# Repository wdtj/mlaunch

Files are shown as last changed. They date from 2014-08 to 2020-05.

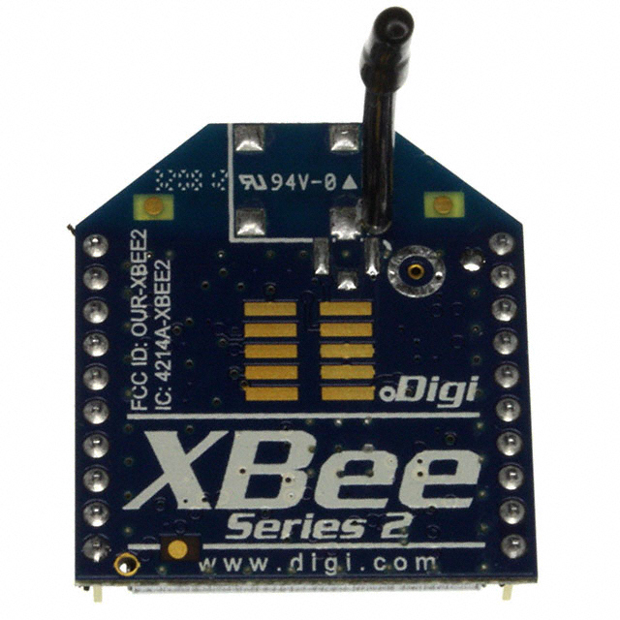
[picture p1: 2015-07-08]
XB24-Z7WIT-004.JPG

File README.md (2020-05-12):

# mLaunch launch control system

mLaunch is a mesh network based model rocket launch system designed to handle up to 8 launch pads.  Its primary feature is safety.  Multiple commands are required to enable multiple relays in the launch circuit.  It also provides feedback on igniter resistance and battery voltage.  Using a mesh network, allows near launch pads to relay launch commands to launch pads further away.

See file Report on [Project mLauch Version 3.0.pdf](Report%20on%20Project%20mLauch%20Version%203.0.pdf) for an overview of mLaunch

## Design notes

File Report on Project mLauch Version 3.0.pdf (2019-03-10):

Wayne Johnson
CSCI5991-001
ID #4348421
joh09024@umn.edu
Independent Study
6/20/2017

# Report on Project mLauch Version 3.0

## Introduction

Did you ever play with model rockets as a kid? It’s a fun hobby that lead to many different areas of Science, Technology, Engineering, and Math (STEM). Building and flying a rocket can involve kinematics (the branch of physics involving motion), aerodynamics, chemistry (as in rocket fuel), even electronics and software engineering as well as many manufacturing technologies. This project is based in the areas of electronics and software development.

A typical model rocket is shown in Figure 1. The rocket has a motor that uses black powder (AKA gun powder) or on larger rockets, Ammonium Perchlorate Composite Propellent (APCP), the same rocket propellent the Space Shuttle used. It also uses a parachute or streamer to help recover the rocket and fins to keep it stable during flight. When the rocket flies to it’s highest altitude, a small ejection charge in the end of the motor pops off the nose cone and deploys the parachute.

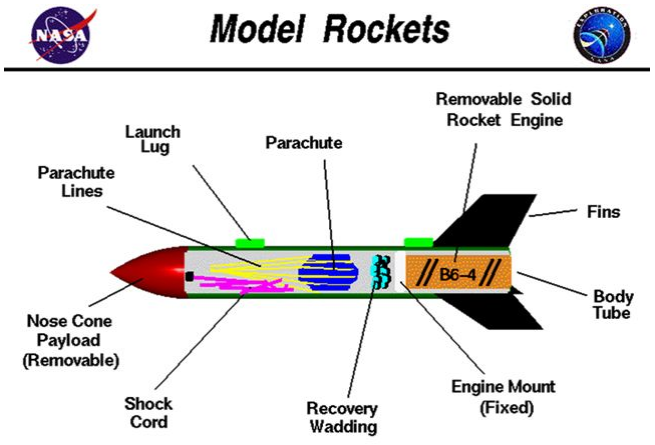
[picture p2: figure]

Figure 1 - Typical Model Rocket

Model rocketry has also grown up with the times. In years past, flying a “Big Bertha” on a class “C” engine was just about the peak of power in the sport. Nowadays, model rockets have developed into high power rocketry. High power rockets as large at 29 feet tall being powered by class “M” class engine have become quite common to the adult high power rocket hobby. To put things in perspective, each letter in the engine classification system is twice as large as the previous. This can lead to an “M” engine that produces as much as 2500 pounds of thrust, and weighing in (just the motor) at 5302.00 grams (12 pounds for the metrically challenged).

As an example of one such rocket launch: Locomotive Breath (a reference to a Jethro Tull song). This rocket was built out of a 16 gauge aluminum pipe and 18 gauge aluminum fins, a single use “P” rocket engine, a pair of parachutes, and a significant amount of on-board electronics such as altimeters and radio tracking equipment. The preflight modeling indicated that it would reach 17,000 feet, while reaching mach 2.3. Figure 2 is picture at launch, the rocket in flight, and what remained after a mid flight failure (as around Mach 1). A post-mortem indicated that one of the fins sheared off in mid flight.

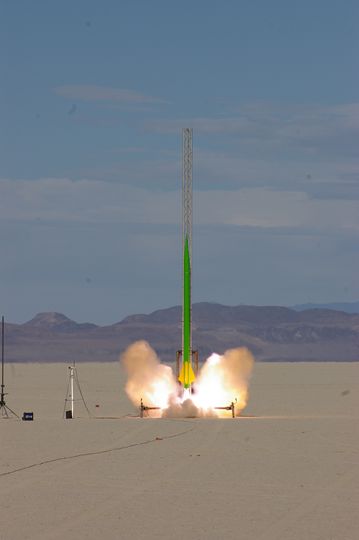
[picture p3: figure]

Figure 2 - Locomotive Breath

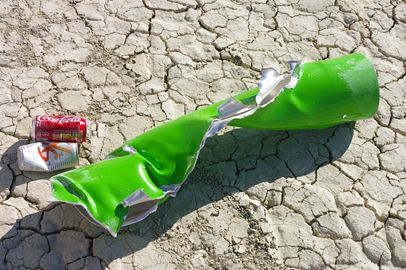
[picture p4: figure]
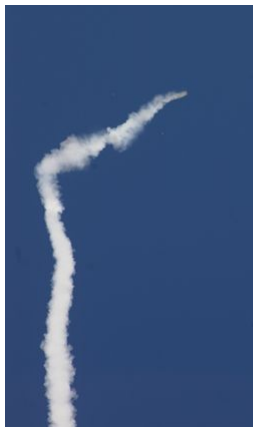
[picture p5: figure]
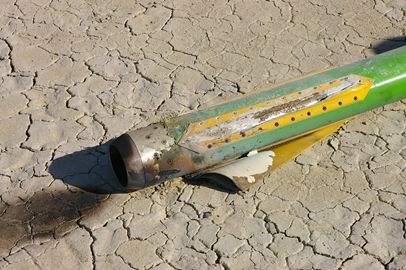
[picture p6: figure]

As you can see, high power rocketry can be hazardous. It is the goal of Tripoli Rocketry Association, as well as the National Association of Rocketry (NAR) to keep the sport safe, as well as fun. Both organizations represent over 10,000 model and high power rocketry enthusiasts around the globe.

You can not simply walk up to a rocket and flick your BIC under the engine. Rocket engines are ignited electronically, by running current through a thin nichrome wire installed in the engine core. The heated wire ignites a small amount of pyrogen, which in turn ignites the rocket fuel. Figure 3 depicts a simple launch system.

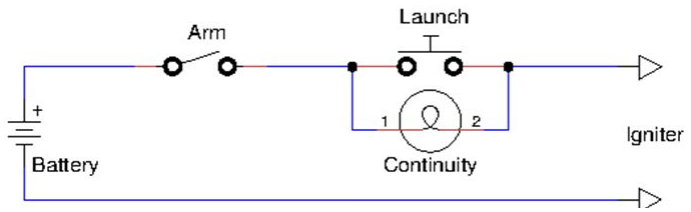
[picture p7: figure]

Figure 3 A Simple Launch System

Because of these dramatic increases in scale in high power rocketry, new safety procedures have been developed. It’s quite common for an class M motor based rocket to be launched 1/4 mile (or more) away from the nearest human or structure. Many different schemes have been used to perform this. Everything from running a 1/4 mile long wire out to the rocket, to using radio control airplane parts. One person used a garage door remote control as a means of closing a relay at the launch pad, to light their rocket. There are been many other schemes, some quite a bit more problematic and unsafe as well. As you can see, there is room for improvement. The mLaunch project was launched to create a safe, dependable, and low cost solution to this problem.

## History of mLaunch

The first version of mLaunch (1.0) was developed in 2004 to augment and eventually replace the launch control system used by Tripoli Minnesota, a local high power rocketry club. For the previous 15 years, Tripoli Minnesota had been using a wired relay based launch controller that included a control panel with toggle switches, a long and heavy wire cable, and remote relay boxes for pads located farther away. A high level overview of this system can be seen in Figure 4.

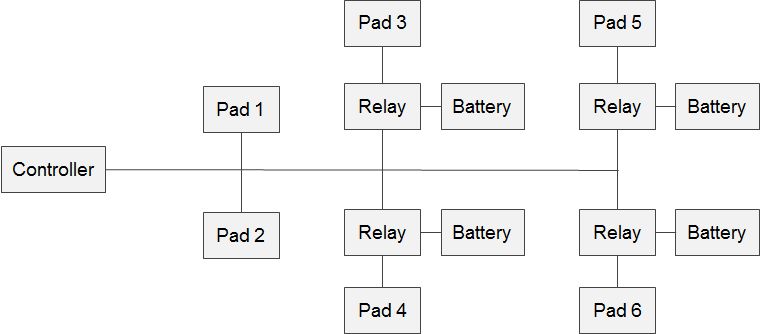
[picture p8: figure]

Figure 4 - Tripoli Wired Launch System

The wired launch system presented several problems. Besides being big and cumbersome to set up, having a 40 lb spool of wire, it also had many points of failure, batteries being low, connections being bad, relay contacts getting worn. It also had limited ways of diagnosing an issue. Many times club members would be seen probing around the pads with a volt meter trying to identify just why their rocket wouldn’t go.

### mLaunch 1

At this point, two new technologies were making it to market. Cheap and easy to program single chip microcomputers, and a new Maxstream XBee wireless module based on the Zigbee mesh network protocol. These two technologies were put together to create a wireless launch system. At the pad end, a XBee transceiver (AKA Modem), an Atmel ATMega8

System-on-a-Chip, push-button switches and LEDs to check for igniter continuity, and a pair of relays to actually launch the rocket.

At the Launch Controller end, is another XBee transceiver and ATMega8 as well as push buttons, and LEDs to show status of the pads. See Figure 5.

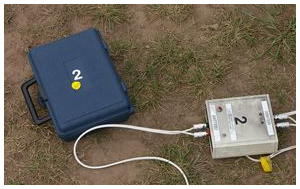
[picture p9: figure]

Figure 5 - Version 1 pad box.

As a first attempt, this system worked quite well and remained in production for over 7 years. It’s still around and servers as a backup system. Unfortunately the system was built using home made printed circuit boards (many of which had to be patched due to etching flaws, as well as a “rats nest” of wired interconnections between PC board and relays, LEDs, push-buttons, and banana jacks (for power and pad connections). With the desire to make the system easier to manufacture, version 2 was planned.

### mLaunch 2

mLaunch2 brought many new production class enhancements. It was a first attempt at surface mount technology, used professionally made PCBs, Digi (which bought out MaxStream) XBee Series 2 modules, and a Atmel Dragon JTAG & IDE programmer/debugger. Many factors combined to doom this version, the XBee Series 2 modules were buggy, the new SMT technology had a large learning curve, and the ATMega8 chip was cramped for RAM space leading to stack corruption and some very frustrating and confusing software failures. The project got shelved.

### mLaunch 3

Knowing the end-of-life was approaching for the version 1 system, a fresh start was made on a new version 3 in 2012. This new design included more SMT parts, a bigger Atmel Mega32 Series CPU, A new PCB Supplier (the earlier one went out of business), a new Atmel ICE/JTAG3 professional class programmer & IDE.

This version was completed, and programmed, and put into production in the spring of 2014.

## mLaunch 3.0 Requirements

Some of the requirements for mLaunch 3.0 were (and still are):

- Easy to make, single board construction
- Minimal circuit connections, no rats nests or wiring harness
- More reliable components
- Dual automotive grade relays which are field replaceable
- 20 amp automotive class circuit breaker instead of fuses to protect from igniter (and other) short circuits.
- Reverse voltage protection & static “surge” protection
- More detailed remote statistics such as actual ignitor resistance and pad end battery voltage via a 8x20 LCD to display
- Dual circuit per pad box (to reduce costs)
- 8 Pad support
- CPU powers up in inert state preventing accidental relay closures when started.
- Ultra bright tri-color (red/green/yellow) LEDs, 180-450 lumen, visible in direct sunlight (most of the time).

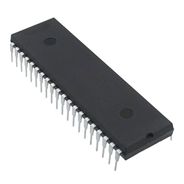
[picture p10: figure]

## ATMega32A CPU Specification Highlights

- Up to 16MIPS Throughput at 16MHz
- 32Kbytes of In-System Self-programmable Flash Program Memory
- 1024Bytes EEPROM
- 2Kbytes Internal SRAM
- Two 8-bit Timer/Counters, One 16-bit Timer/Counter
- 32 Programmable I/O Lines
- 8-channel, 10-bit ADC
- Programmable Serial USART
- $5.88 MSRP

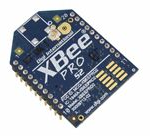
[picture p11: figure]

## XBee-Pro™ ZB S2B Specification Highlights

- 2.4 GHz Transceiver (Transmitter/Receiver)
- Extended-range ZigBee, Through-hole, Mesh Networking
- 2 miles / 3.2 km Range (YMMV, outdoors, with a parabolic antenna, and the wind at your back). Expect 1/4 mile.
- $28.00 MSRP
- 250 Kbps Data Rate

## Mesh Networking

Unlike the MaxStream XBee Series 1, the Digi XBee Series 2 supports true mesh networking. This means that if a node in the network receives a message for some other node, it will pass that message on to it’s nearest neighbor that is nearer to the final destination. Using a mesh network in mLaunch allows us to place launch pads out of the direct range of the launch controller, but as long as there are one or more nodes (i.e. pads) connected between the controller and the remote pads, command and status messages can still be sent. This is represented in Figure 6

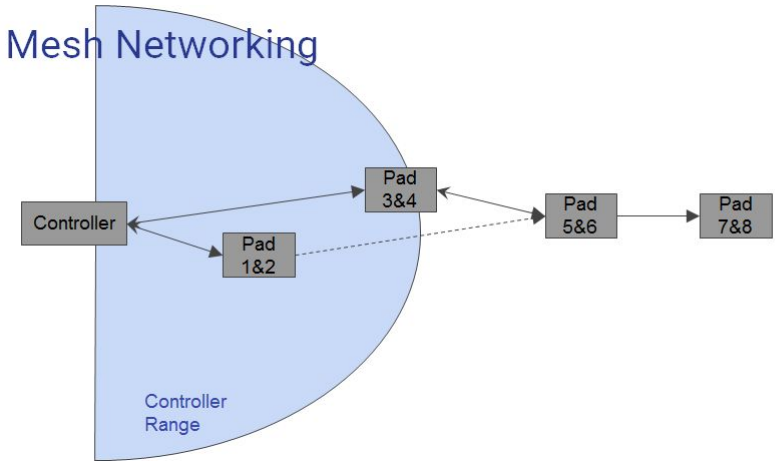
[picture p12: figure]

Figure 6 - mLaunch Mesh network

## Block Diagrams

The mLaunch system consists of two types of modules. One Launch Controller box, and up to 4 pad boxes.

### Launch Controller

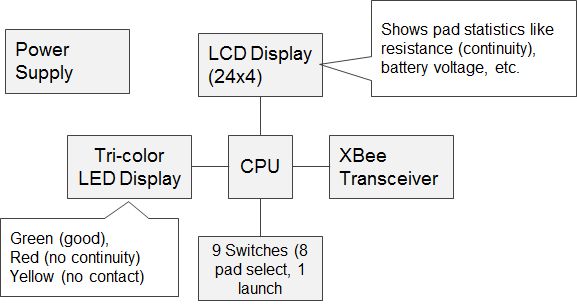
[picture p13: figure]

Specific schematics for the Launch Controller are available at https://github.com/wdtj/mlaunch/blob/master/controller30/controller30r3.pdf

Power Supply
The mLaunch Launch Controller power supply is pretty standard. It accepts 6-18 volts input and provides both regulated 3.3 and regulated 5 volt outputs. One interesting note is that the input to the power supply contains a bridge diode. A bridge diode is normally used to rectify AC inputs into DC. Using in here allows the Launch Controller to be mis-connected to a battery and it will still work. Also included in the input circuit is an 18v varistor to protect the circuit from static discharge along the power input path.

CPU
The mLaunch launch controller CPU is an Atmel ATMega32A microprocessor on a chip. The CPU runs off the 5 volt power supply and uses a 16Mhz crystal for a CPU clock. Although the ATMega32A has a built in capacitive clock circuit, it is not accurate enough to control the serial communications connection with the XBee module at 9600 baud. In addition, the ATMega32 is connected to a 10 pin 1mm pitch header. This is used for programming the CPU as well as debugging. Details on the ATMega CPU architecture and programming are available in the ATmel supplied ATMega32 documentation at https://github.com/wdtj/mlaunch/blob/master/atmega32A.pdf.

XBee Transceiver
The XBee transceiver is the heart of the system communications. These modules are pre-programmed with either XBee coordinator or router software. There can be only one coordinator in the XBee network, and this device coordinates the mesh network. The XBee uses a 3.3 volt power supply. In order to translate between the CPU’s 5 volt signals and the XBee 3.3 volt signals a simple voltage shifter is used. By default the XBee operate at 9600. The module is also preprogrammed to run in API command mode (vs AT command mode) to make it easier to communicate with the CPU. Details on the XBee communication commands and other details are available in the Digi supplied XBee user’s guide at https://github.com/wdtj/mlaunch/blob/master/XBeePro2.pdf. Connection to the XBee transceiver is via the CPU’s USART on the RXD and TXD pins.

LCD Display
The LCD display is a LCM-S02004DSR from
Lumex. Pinout and electrical specs are here:

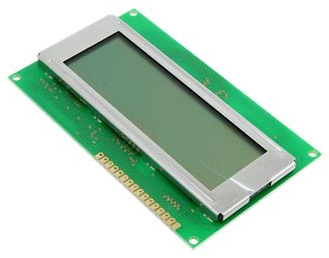
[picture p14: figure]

https://github.com/wdtj/mlaunch/blob/master/LCM-S02004DSR.pdf
It uses an industry standard LCD controller HD44780U. You can find this spec at https://github.com/wdtj/mlaunch/blob/master/HD44780.pdf The LCD requires 5 volt power and 5 volt data signals, but since the CPU is already running at 5 volts this is not an issue. The LCD uses 8 parallel lines to send data/address information to/from the LCD display, along with 3 control lines. The CPU port PA 8 bit port provides the basic parallel data, and the CPU’s PD2, PD3, and PD4 lines provide control signals. Basically a command or data byte is written on the PA port and the E pin is strobed to send data to the LCD. Consult the HD44780 document for more specific details.

Switches
9 pushbutton switches are connected directly to input pins of the CPU. These are pulled high (a logic 1 state) by internal (to the CPU) resistors, and pressing one of the buttons causes the input to be grounded (pulled low) to present a 0. Software needs to “debounce” these switches because the mechanical contacts in the switch can vibrate on contact producing an intermittent signal for a few milliseconds. The software, when detecting a switch that is opened or closed will need to check again a few milliseconds later to verify it’s still in that state. The pad enable switches use the CPU’s PB port (8 pins) and the PC7 pin for the launch button.

LEDS
The LEDs have 3 different LED circuits in one package. Red, green, and yellow. This amounts to 24 different circuits required to drive all LEDs, more than are available on the CPU. To get around this, there are 3 TI TLC5917 LED drivers in the circuit. This driver is basically 3 8 bit shift registers, wired in series. To turn on or off an LED, the appropriate bit is output into the input (SDI) of the first driver register and the driver clock signal (CLK) is strobed. Then the next bit, etc. until all 24 bits have been written. All the red LEDs are written in the first byte, all yellow on the second byte, and all green in the third byte of the 24 bits. Specifications for the TLC5917 driver can be found at https://github.com/wdtj/mlaunch/blob/master/tlc5917.pdf. The LED driver is connected to the CPU’s PD5 (CLK), PD6 (LE), PD7 (SDI), and PC0 (SDO) pins.

## MLaunch Pad

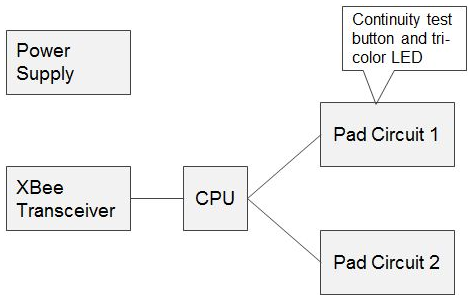
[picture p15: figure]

Specific schematics for the Pad is available at https://github.com/wdtj/mlaunch/blob/master/pad30/pad30r4.pdf

Each pad modules is capable of managing 2 pads and thus has 4 relays (2 per pad), 2 continuity test buttons, and 2 tri-color LEDs as well as circuitry to measure the voltages across the ignitor and a circuit to measure battery voltage.

Power Supply
The mLaunch Pad power supply is also pretty standard. It accepts 6-18 volts input and provides regulated 3.3 volt output. Again the power supply contains a bridge diode to allow the battery inputs to be mis-connected and also it has an 18v varistor to protect the circuit from static discharge along the power input path. One interesting problem in development, the diode bridge can allow the voltage sensing circuit for the pads ignition to be either above or below the ground voltage of the CPU and it’s integrated ADC. This issue is handled by a set of resistors in that circuit that translate the voltages from the possible +18 to -18 volts to the ADC’s required 0-2.55 volts.

CPU
The mLaunch pad CPU is again an Atmel ATMega32A microprocessor on a chip. The CPU runs off the 3.3 volt power supply and it uses a 16Mhz crystal for a CPU clock. Everything else is the same as for the launch controller. The CPU circuit also contains a resistor bridge that allows the CPUs ADC to measure the battery voltage.

XBee Transceiver
The pad transceivers are preprogrammed as router nodes. Since both the XBee and CPU uses a 3.3 volt power supply no translation is needed. Connection to the XBee transceiver is via the CPU’s USART on the RXD and TXD pins.

Pad Circuit
The pad circuit (x2) contains a ULN2003A darlington transistor driver, which provides enough current to the CPU signal to drive the relay coils. These also protect the CPU from high reverse EMF pulses that are generated as the relays turn off. A network of resistors translate the possible +18 volt to -18 volt continuity signal from the pad into a 0-2.55 volt signal for the CPUs ADC.

In addition, each pad circuit contains a pushbutton switch to test continuity and a tri-color LED to display the results. The pad controls use the following pin assignments:

Function | Pad 1 CPU Pin | Pad 2 CPU Pin
Continuity Detect ADC Input | PA0/ADC0 | PA1/ADC1
BATT+ ADC Input | PA2/ADC2 | PA2/ADC2
Launch Relay | PA3 | PA6
Enable Relay | PA4 | PA7
Red LED | PB0 | PB4
Green LED | PB1 | PB5
Yellow LED | PB2 | PB6
Continuity Switch | PB3 | PB7

## Functional Overview

In order to launch a rocket, first the rocket owner places the rocket on the pad, and connects the pad’s ignition leads to the ignitor in the rocket engine. The owner can then press the pad’s continuity button which will light up green (good continuity) or red (red continuity). There is also a yellow light that indicates low battery voltage.

When the Launch Control Officer (LCO) gets ready to launch the rocket, they press and release a button on the launch controller corresponding to the appropriate pad. The pad’s first relay closes in order to place a small continuity test current through the ignitor. Both the pad and launch controller LEDs light with the continuity status. The LCO then presses the launch button which closed the second relay at the pad. This sends the full battery current through the igniter. When the LCO releases the launch button, the pad is then disabled.
If, before pressing the launch button, the LCO presses the pad enable button a second time, the pad is disabled and returns to it’s initial state..

If, before pressing the launch button, the LCO presses the a second (or more) pad enable button those pads are enabled and their respective LEDs light with their statuses. Then by pressing the launch all the enabled pads are launched.

If, when pressing the pad enable button the first time it’s held down for more than a second, the pad statistics (battery voltage and continuity resistance) are displayed on the LCD display.

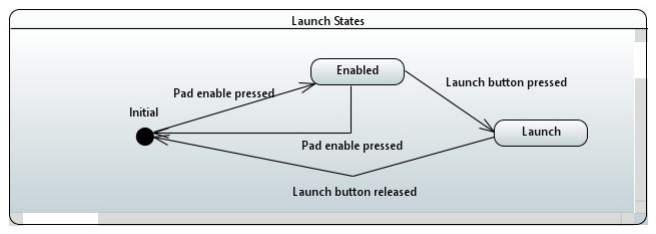
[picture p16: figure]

## Application Level Message Packets

There are relatively few application level packets exchanged. They are kept short to reduce requirements on bandwidth. They do not have any CRC or other error checking/correcting data as these functions are done in the XBee itself. These packets include:

Enable - Enable the continuity checking relay and causes the pad to begin to send back status packets. | Ex where x is a pad number from 1-8
Launch - Closes the launch relay | Lx where x is a pad number from 1-8
Status - Returned by the pad with current information | Sxnn...n where x is a pad number from 1-8, and nn...n is pad status information
Unlaunch - Opens the launch relay | Ux where x is a pad number from 1-8
Disable - Opens the continuity relay and return to normal state. | Dx where x is a pad number from 1-8
Identify - Caused the specified pad to begin flashing it’s green LEDS to identify it for configuration. | I
Assign - Assigns a pad number to that pad. Used for configuration. | Ax where x is a pad number from 1-8

After an Enable command is sent, a watchdog timer is set that will reset the pad if no other request is sent within 10 seconds. This timer is restarted when any packet is received for that pad. To ensure a pad does not reset itself too early, the controller repeats the enable command every second. After a pad receives an Enable message, it begins sending back Status messages every second until the Disable message is received or the watchdog timer resets the pad.

The watchdog timer is used to safe any and all pads in the event the Launch Controller goes away.

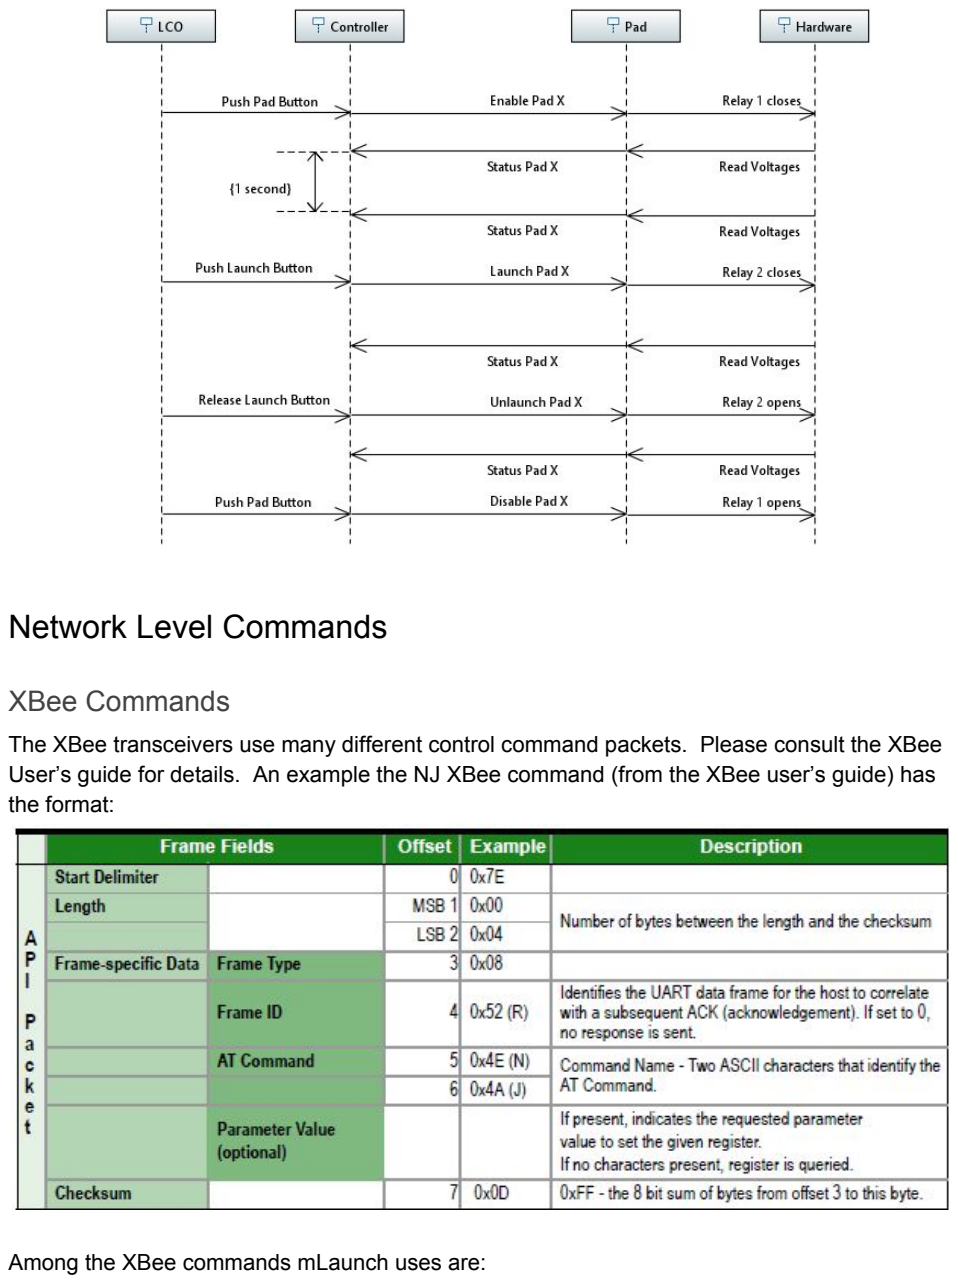
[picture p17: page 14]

## Network Level Commands

### XBee Commands

The XBee transceivers use many different control command packets. Please consult the XBee User’s guide for details. An example the NJ XBee command (from the XBee user’s guide) has the format:

Among the XBee commands mLaunch uses are:

NI | Node Identifier. Set/read a string identifier naming the node.
NJ | Node Join Time. Set/Read the time that a Coordinator/Router allows nodes to join.
NR | Network Reset. Reset network layer parameters on all modules within a network.
ND | Node Discover. Discovers and reports all RF modules found.
NJ | Node Join Time. Set/Read the time that a Coordinator/Router allows nodes to join.
JV | Channel Verification.
VR | Firmware Version. Read firmware version of the module.
JN | Join Notification. Set / read the join notification setting. If enabled, the module will transmit a broadcast node identification packet on power up and when joining.

When the system if first brought up, the Launch Controller initializes all it’s hardware and sends a command to the XBee module to discover it’s network (all the pads). Over the next 5 seconds each powered up pad responds with it’s name and a network address. The XBee devices randomly staggers the responses to prevent everyone from answering the discovery broadcast at once. As each pad is identified, the Launch Controller LEDs for that pad set are turned green. When the 5 second wait is done, the controller turns off all the LEDs and is ready for business.

During operation, if any pad joins the network, the Launch Controller will receive a Discovery notification from the XBee device and add that pad to it’s operational list.

### XBee Data

In addition to commands sent to the XBee transceiver, application data is sent. Data is wrapped in a XBee API data packet. These data packets can then be marked to be sent to a specific node using a XBee Explicit Addressing ZigBee Command Frame, or can be sent to all devices. All communications are via explicit addressing

## Software Design

The ATMega system are very minimal. They do not contain an operating system, therefore all software is written on “bare metal” and in machine code. To this end, the majority of the software is asynchronous in nature, operating on a set of Finite State Machines (FSM). When a packet is to be sent to the XBee transceiver, the message is queued up and the USART’s interrupt system then controls when the next character is to be sent. There is also a FSM managing pad controls, switch closure detection (debouncing), and the communication protocol to the XBee.

### Modules

Software is broken into the following “projects” or modules: Utilities
Pad
Controller

Utilities
The Utilities module contains common code and drivers including the following:
ADC Driver | Driver for the ATMega internal Analog to Digital Converter
LED Driver | For use with the TI TLC5917 LED drivers
OLED/LCD Driver | For use with the Lumenx (and other) LCD module
Timer0/Timer1 Driver | Driver for the ATMega internal timers
UART Driver | Driver for the ATMega internal USART
XBee Diver | Driver for the XBee module (connects through the UART Driver)

Pad

Hardware Initialization | Sets ATMega Input/Output configuration, initializes required drivers
Pad module | Main
Launch FSM | FSM to manage launch status, processes Launch Controller commands
Link FSM | Manages XBee initialization and communications
Status FSM | Maintains Pad status and sends status information

Switch FSM | Debounces switches

Controller

Hardware Initialization | Sets ATMega Input/Output configuration, initializes required drivers
Controller module | Main
Link FSM | Manages XBee initialization and communications
Switch FSM | Debounces switches

## To do

Additional items for future releases include these features.

- Encryption (feature of the Xbee module)
- Voltage profile at launch. Did ignition cause the battery/igniter voltage to drop?
- Software configuration safety.
- Network routing information and field strengths on LCD.

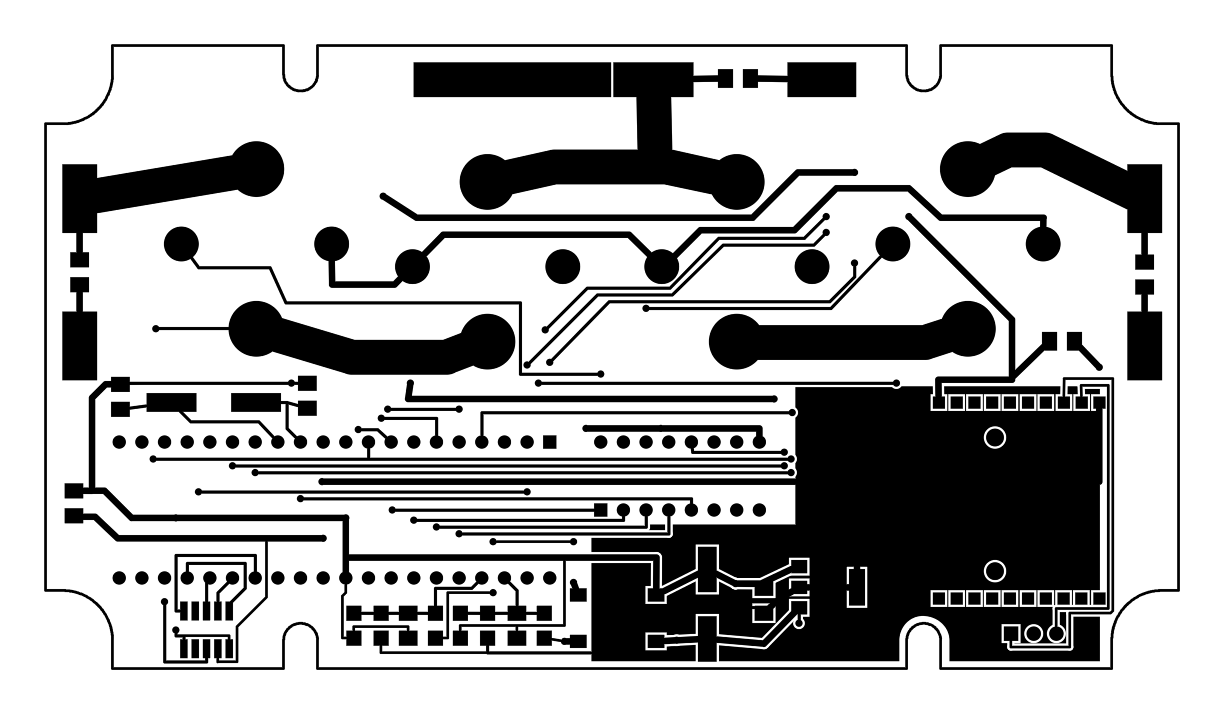
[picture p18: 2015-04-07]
pad30/CAM/top_copper.png

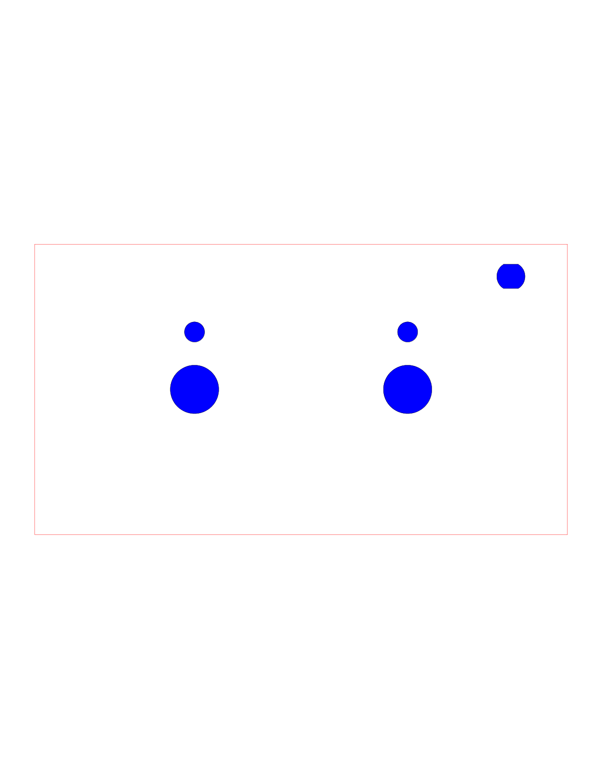
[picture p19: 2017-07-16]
pad30/pad-panel-markup.png

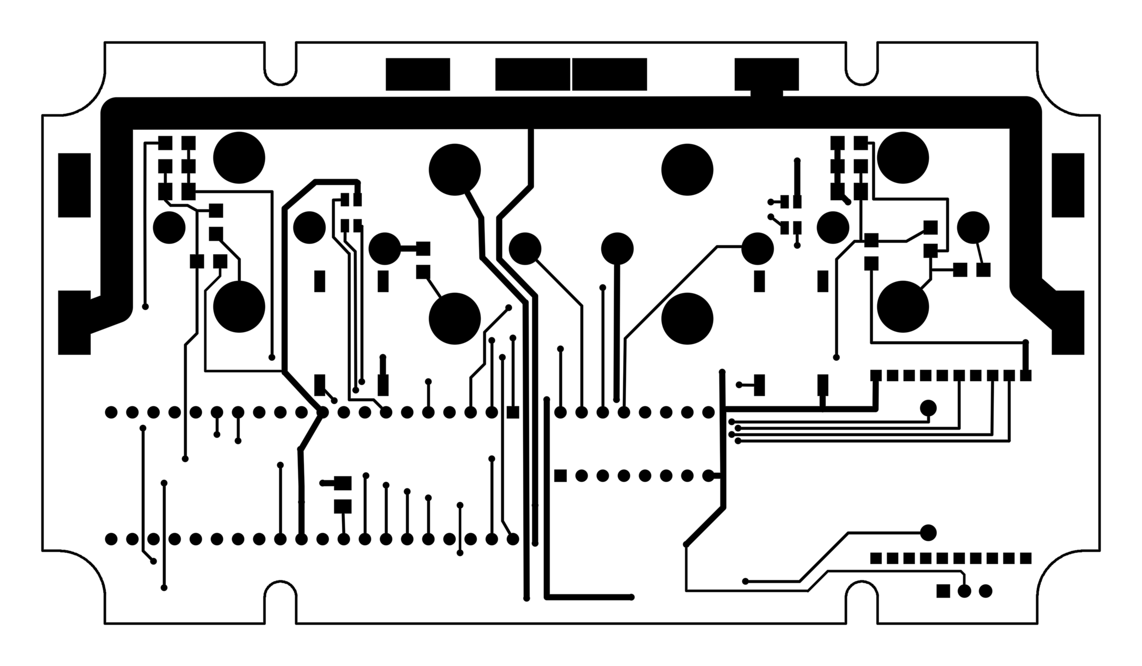
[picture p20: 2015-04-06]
pad30/CAM/bottom_copper.png

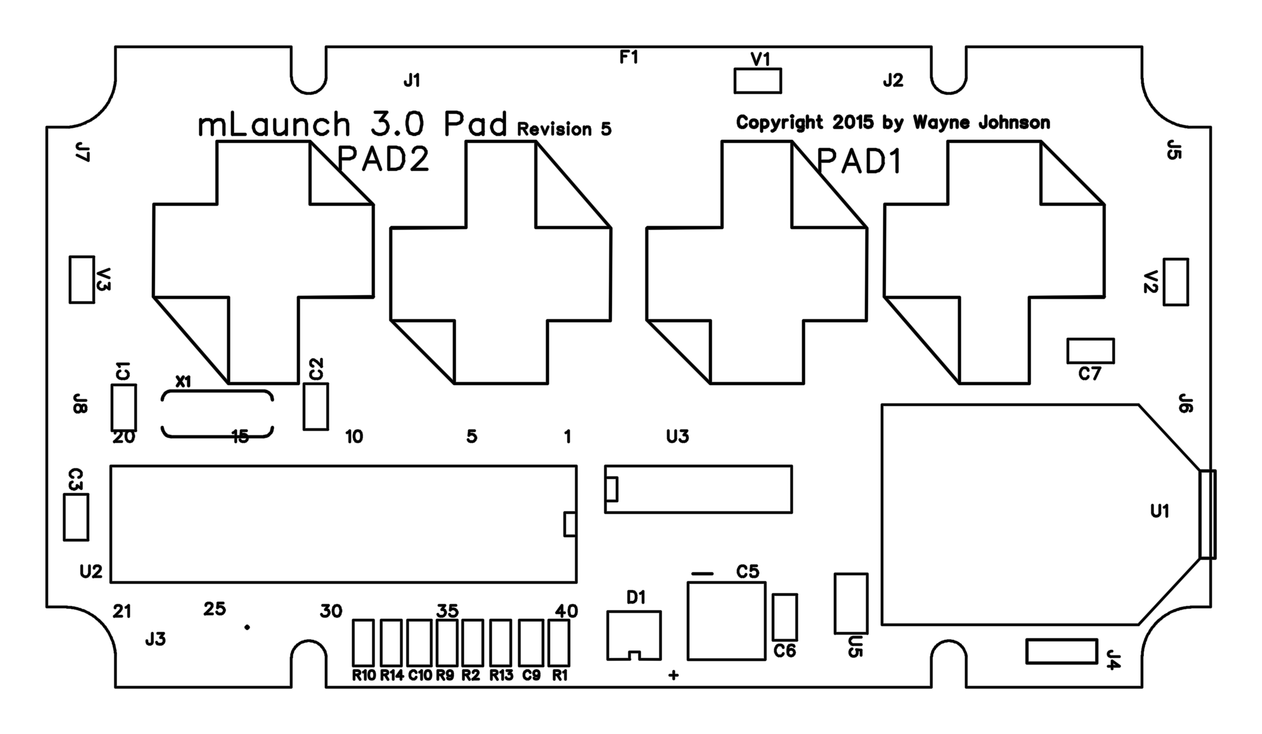
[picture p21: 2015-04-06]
pad30/CAM/top_silk.png

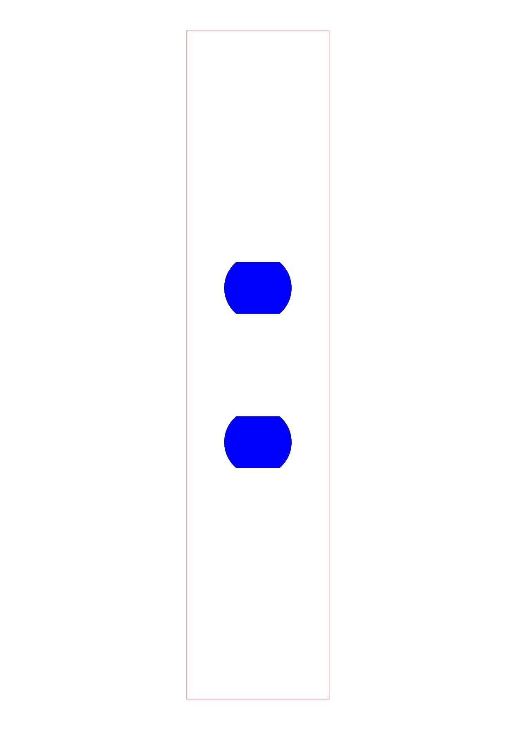
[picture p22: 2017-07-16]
pad30/pad-side-markup.png

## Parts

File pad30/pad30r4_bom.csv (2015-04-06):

Digi-Key Part Number | Manufacturer | Manufacturer Part Number | Customer Reference | Quantity 1 | Quantity 2 | Quantity 3 | Mfg Std Lead Time | Description | Comments | RoHS Status | Lead Free Status | REACH Status
J152-ND | CINCH CONNECTIVITY SOLUTIONS JOHNSON | 108-0903-001 | BANANA JACK 1,BANANA JACK 2,BANANA JACK 3 | 3 | 0 | 0 | 6 Weeks | CONN JACK BANANA INSUL NYLON BLA |  | RoHS Compliant | Lead free | N/A
609-3470-ND | FCI | 68001-203HLF | J4 | 1 | 0 | 0 | 6 Weeks | BERGSTIK II .100" SR STRAIGHT |  | RoHS Compliant | Lead free | Unaffected Dec-2012
302-1242-ND | E-T-A | 1610-92-10A | F1 | 1 | 0 | 0 | 8-9 Weeks | CIR BRKR THRM 10A 12VDC |  | RoHS Compliant | Lead free | Unaffected Jun-2014
S5751-10-ND | SULLINS CONNECTOR SOLUTIONS | NPPN101BFCN-RC | J13,J14 | 2 | 0 | 0 | 2-4 Weeks | CONN RECEPT 2MM SINGLE STR 10POS |  | RoHS Compliant | Lead free | Unaffected Dec-2013
3M5475-ND | 3M | 4816-3004-CP | J16 | 1 | 0 | 0 | 6 Weeks | CONN IC DIP SOCKET 16POS TIN |  | RoHS Compliant | Lead free | Not Available
S9013E-05-ND | SULLINS CONNECTOR SOLUTIONS | GRPB052VWQP-RC | J3 | 1 | 0 | 0 | 2-4 Weeks | CONN HEADER .050" 10PS DL SMD AU |  | RoHS Compliant | Lead free | Unaffected Dec-2013
311-1.00MFRCT-ND | YAGEO (VA) | RC1206FR-071ML | R13,R14,R5,R8 | 4 | 0 | 0 | 17 Weeks | RES SMD 1M OHM 1% 1/4W 1206 | Alternate Packaging Exists | RoHS Compliant | Lead free | Unaffected Jun-2014
311-56.2KFRCT-ND | YAGEO (VA) | RC1206FR-0756K2L | R10,R2,R4,R7 | 4 | 0 | 0 | 17 Weeks | RES SMD 56.2K OHM 1% 1/4W 1206 | Alternate Packaging Exists | RoHS Compliant | Lead free | Unaffected Jun-2014
679-2226-ND | MEC SWITCHES | 3FSH9 | S1,S2 | 2 | 0 | 0 | 12-14 Weeks | SWITCH TACTILE SPST-NO 0.05A 24V |  | RoHS Compliant | Lead free | Unaffected Dec-2013
296-1979-5-ND | TEXAS INSTRUMENTS | ULN2003AN | U3 | 1 | 0 | 0 | 6 Weeks | TRANS 7NPN DARL 50V 0.5A 16DIP | Alternate Packaging Exists | RoHS Compliant | Lead free | Unaffected Jun-2012
609-4716-ND | FCI | DILB40P-223TLF | J15 | 1 | 0 | 0 | 7 Weeks | CONN IC DIP SOCKET 40POS TIN |  | RoHS Compliant | Lead free | Unaffected Dec-2012
0600-00039-ND | LAIRD - EMBEDDED WIRELESS SOLUTIONS | 0600-00039 | A1 | 1 | 0 | 0 | 8 Weeks | ANTENNA 2.45GHZ 7" RA U.FL PLUG |  | RoHS Compliant | Lead free | Unaffected Aug-2011
PB679-ND | TE CONNECTIVITY POTTER & BRUMFIELD | 1432782-1 | K1,K2,K3,K4 | 4 | 0 | 0 | 10 Weeks | RELAY AUTOMOTIVE SPST 30A 12V |  | RoHS Compliant | Lead free | Unaffected Aug-2011
458-1088-ND | MALLORY SONALERT PRODUCTS INC | MSR516NR | B1 | 1 | 0 | 0 | 6 Weeks | BUZZ PIEZO CIRC 23MM RADIAL |  | RoHS Compliant | Lead free | Unaffected Jun-2014
1287K-ND | KEYSTONE ELECTRONICS | 1287 | J1,J2,J5,J6,J7,J8 | 6 | 0 | 0 | 4 Weeks | CONN QC TAB 0.250 SOLDER |  | RoHS Compliant | Lead free | Unaffected Jun-2014
3525K-ND | KEYSTONE ELECTRONICS | 3525 | J17,J18 | 2 | 0 | 0 | 4 Weeks | CONN QC RCPT 0.205 PRESS-FIT |  | RoHS Compliant | Lead free | Unaffected Jun-2014
AP1117IE33G-13DICT-ND | DIODES INCORPORATED (VA) | AP1117IE33G-13 | U5 | 1 | 0 | 0 | 18 Weeks | IC REG LDO 3.3V 1A SOT223-3 | Alternate Packaging Exists | RoHS Compliant | Lead free | Unaffected Jun-2014
602-1101-ND | DIGI INTERNATIONAL | XBP24-Z7UIT-004 | U1 | 1 | 0 | 0 | 6 Weeks | MODULE ZIGBEE-PRO W/U.FL ANT | No delivery date available | RoHS non-compliant | Contains lead | Not Available
J151-ND | CINCH CONNECTIVITY SOLUTIONS JOHNSON | 108-0902-001 | BANANA JACK 4,BANANA JACK 5,BANANA JACK 6 | 3 | 0 | 0 | 6 Weeks | CONN JACK BANANA INSUL NYLON RED |  | RoHS Compliant | Lead free | N/A
ATMEGA32A-PU-ND | ATMEL | ATMEGA32A-PU | U2 | 1 | 0 | 0 | 9 Weeks | IC MCU 8BIT 32KB FLASH 40DIP |  | RoHS Compliant | Lead free | Unaffected Dec-2013
PB232-ND | TE CONNECTIVITY POTTER & BRUMFIELD | VCF4-1000 | J10,J11,J12,J9 | 4 | 0 | 0 | 10 Weeks | SOCKET RELAY PC MNT FOR VF4 SER |  | RoHS Compliant | Lead free | Unaffected Aug-2011
SR153A-ND | SERPAC | 153,AL | E1 | 1 | 0 | 0 | 2 Weeks | BOX 5.62X3.25X2.50 ALMOND |  | RoHS Compliant | Lead free | Unaffected Oct-2011
8911K-ND | KEYSTONE ELECTRONICS | 8911 | LED SPACER 1,LED SPACER 2 | 2 | 0 | 0 | 4 Weeks | SPACER MOUNT LED TRI-LEAD .320" |  | RoHS Compliant | Lead free | Unaffected Jun-2014
754-1232-ND | KINGBRIGHT COMPANY LLC | WP59EGW | D2,D3 | 2 | 0 | 0 | 6-7 Weeks | LED IND 5MM RED/GRN WHT DIFF |  | RoHS Compliant | Lead free | Unaffected Jun-2014
311-1222-1-ND | YAGEO (VA) | CC1206DRNPO9BN8R2 | C7 | 1 | 0 | 0 | 17 Weeks | CAP CER 8.2PF 50V NPO 1206 | Alternate Packaging Exists | RoHS Compliant | Lead free | Unaffected Jun-2014
641-1344-5-ND | COMCHIP TECHNOLOGY | DF005S-G | D1 | 1 | 0 | 0 | 10 Weeks | RECT BRIDGE GPP 50V 1A DFS |  | RoHS Compliant | Lead free | Unaffected Dec-2013
311-1.00KFRCT-ND | YAGEO (VA) | RC1206FR-071KL | R15,R16,R17,R18 | 4 | 0 | 0 | 17 Weeks | RES SMD 1K OHM 1% 1/4W 1206 | Alternate Packaging Exists | RoHS Compliant | Lead free | Unaffected Jun-2014
PCE4705CT-ND | PANASONIC ELECTRONIC COMPONENTS (VA) | EEE-HAE101UAP | C5 | 1 | 0 | 0 | 21 Weeks | CAP ALUM 100UF 25V 20% SMD | Alternate Packaging Exists | RoHS Compliant | Lead free | Not Available
XC569CT-ND | ECS INC (VA) | ECS-80-S-5P-TR | X1 | 1 | 0 | 0 | 10 Weeks | CRYSTAL 8MHZ SERIES SMD | Alternate Packaging Exists | RoHS non-compliant | Contains lead | Unaffected Jun-2014
311-1466-1-ND | YAGEO (VA) | CC1206KKX5R8BB106 | C3,C6 | 2 | 0 | 0 | 18 Weeks | CAP CER 10UF 25V 10% X5R 1206 | Alternate Packaging Exists | RoHS Compliant | Lead free | Unaffected Jun-2014
311-1153-1-ND | YAGEO (VA) | CC1206JRNPO9BN200 | C1,C2 | 2 | 0 | 0 | 17 Weeks | CAP CER 20PF 50V 5% NPO 1206 | Alternate Packaging Exists | RoHS Compliant | Lead free | Unaffected Jun-2014
311-301KFRCT-ND | YAGEO (VA) | RC1206FR-07301KL | R1,R3,R6,R9 | 4 | 0 | 0 | 17 Weeks | RES SMD 301K OHM 1% 1/4W 1206 | Alternate Packaging Exists | RoHS Compliant | Lead free | Unaffected Jun-2014
311-1435-1-ND | YAGEO (VA) | CC1206JRX7R9BB104 | C10,C11,C12,C8,C9 | 5 | 0 | 0 | 16 Weeks | CAP CER 0.1UF 50V 5% X7R 1206 | Alternate Packaging Exists | RoHS Compliant | Lead free | Unaffected Jun-2014
732-2549-1-ND | WURTH ELECTRONICS INC (VA) | 82541110 | V1,V2,V3 | 3 | 0 | 0 | 8 Weeks | VARISTOR 18V 200A 1206 | Alternate Packaging Exists | RoHS Compliant | Lead free | Unaffected Sep-2011
A09047-ND | TE CONNECTIVITY AMP | 640909-1 |  | 6 | 0 | 0 | 2 Weeks | CONN QC RCPT 18-22AWG 0.205 | Alternate Packaging Exists | RoHS Compliant | Lead free | Unaffected Aug-2011
679-2203-ND | MEC SWITCHES | 2S09-07.0 |  | 2 | 0 | 0 | 12-14 Weeks | EXTENDER SWITCH 7MM HEIGHT |  | RoHS Compliant | Lead free | Unaffected Dec-2013
679-2172-ND | MEC SWITCHES | 1ZC09 |  | 2 | 0 | 0 | 12-14 Weeks | CAP TACTILE ROUND BLACK |  | RoHS Compliant | Lead free | Unaffected Dec-2013

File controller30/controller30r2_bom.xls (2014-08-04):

Customer Reference | Digi-Key Part Number | Manufacturer | Manufacturer Part Number | Quantity 1 | Quantity 2 | Quantity 3 | Mfg Std Lead Time | Description | Comments | RoHS Status | Lead Free Status | REACH Status
A1 | 0600-00039-ND | LAIRD - EMBEDDED WIRELESS SOLUTIONS | 0600-00039 | 1 | 0 | 0 | 8 Weeks | ANTENNA 2.45GHZ 7" RA U.FL PLUG |  | RoHS Compliant | Lead free | Unaffected Aug-2011
C1 | PCE4705CT-ND | PANASONIC ELECTRONIC COMPONENTS (VA) | EEE-HAE101UAP | 1 | 0 | 0 | 21 Weeks | CAP ALUM 100UF 25V 20% SMD | Alternate Packaging Exists | RoHS Compliant | Lead free | Not Available
C10 | 311-1222-1-ND | YAGEO (VA) | CC1206DRNPO9BN8R2 | 1 | 0 | 0 | 9 Weeks | CAP CER 8.2PF 50V NPO 1206 | Alternate Packaging Exists | RoHS Compliant | Lead free | Unaffected Sep-2011
C2,C3,C4,C5,C8,C9 | 311-1466-1-ND | YAGEO (VA) | CC1206KKX5R8BB106 | 6 | 0 | 0 | 10 Weeks | CAP CER 10UF 25V 10% X5R 1206 | Alternate Packaging Exists | RoHS Compliant | Lead free | Not Available
C6,C7 | 311-1153-1-ND | YAGEO (VA) | CC1206JRNPO9BN200 | 2 | 0 | 0 | 9 Weeks | CAP CER 20PF 50V 5% NPO 1206 | Alternate Packaging Exists | RoHS Compliant | Lead free | Unaffected Sep-2011
D1 | 641-1344-5-ND | COMCHIP TECHNOLOGY | DF005S-G | 1 | 0 | 0 | 8 Weeks | RECT BRIDGE GPP 50V 1A DFS |  | RoHS Compliant | Lead free | Unaffected Dec-2013
D10,D3,D4,D5,D6,D7,D8,D9 | 492-1227-1-ND | BIVAR INC (VA) | SMP4-SRGY | 8 | 0 | 0 | 6 Weeks | LED GREEN/RED/YELLOW CLEAR 4PLCC | Alternate Packaging Exists | RoHS Compliant | Lead free | N/A
ENCL | SR17SA-ND | SERPAC | 17S,AL | 1 | 0 | 0 | 2 Weeks | BOX SLANT ALM (6.88X4.88X2.48) |  | RoHS Compliant | Lead free | Unaffected Oct-2011
J1,J2 | 609-3469-ND | FCI | 68001-202HLF | 2 | 0 | 0 | 6 Weeks | BERGSTIK II .100" SR STRAIGHT |  | RoHS Compliant | Lead free | Unaffected Jun-2011
J3 | 609-3470-ND | FCI | 68001-203HLF | 1 | 0 | 0 | 6 Weeks | BERGSTIK II .100" SR STRAIGHT |  | RoHS Compliant | Lead free | Unaffected Jun-2011
J4,J8 | A26943-ND | TE CONNECTIVITY AMP | 87176-2 | 2 | 0 | 0 | 10 Weeks | CONN HOUSING 2POS .100 LOCK DUAL |  | RoHS Compliant | Request inventory verification | Unaffected Aug-2011
J5 | S9013E-05-ND | SULLINS CONNECTOR SOLUTIONS | GRPB052VWQP-RC | 1 | 0 | 0 | 2-4 Weeks | CONN HEADER .050" 10PS DL SMD AU |  | RoHS Compliant | Lead free | Unaffected Jun-2013
J6,J7 | S5751-10-ND | SULLINS CONNECTOR SOLUTIONS | NPPN101BFCN-RC | 2 | 0 | 0 | 2-4 Weeks | CONN RECEPT 2MM SINGLE STR 10POS |  | RoHS Compliant | Lead free | Unaffected Jun-2013
K1 | 3M5483-ND | 3M | 4840-6004-CP | 1 | 0 | 0 | 5 Weeks | SOCKET IC OPEN FRAME 40POS .6" |  | RoHS Compliant | Lead free | Not Available
Q1 | BSS138CT-ND | FAIRCHILD SEMICONDUCTOR (VA) | BSS138 | 1 | 0 | 0 | 7 Weeks | MOSFET N-CH 50V 220MA SOT-23 | Alternate Packaging Exists | RoHS Compliant | Lead free | Unaffected Jun-2011
R10 | 311-4.99KFRCT-ND THIS PART IS ROHS COMPLIANT. |  |  | 1 | 0 | 0 |  |  | Match Not Found | Not Available | Not Available | Not Available
R3,R4,R5,R6 | 311-10.0KFRCT-ND | YAGEO (VA) | RC1206FR-0710KL | 4 | 0 | 0 | 9 Weeks | RES 10.0K OHM 1/4W 1% 1206 SMD | Alternate Packaging Exists | RoHS Compliant | Lead free | Unaffected Sep-2011
R7,R8,R9 | 311-910FRCT-ND | YAGEO (VA) | RC1206FR-07910RL | 3 | 0 | 0 | 9 Weeks | RES 910 OHM 1/4W 1% 1206 SMD | Alternate Packaging Exists | RoHS Compliant | Lead free | Unaffected Sep-2011
S1,S2,S3,S4,S5,S6,S7,S8,S9 | 679-2219-ND | MEC SWITCHES | 3ESH9-15.0 | 9 | 0 | 0 | 12-14 Weeks | SWITCH TACTILE SPST-NO 0.05A 24V |  | RoHS Compliant | Lead free | Unaffected Jun-2012
S10 | 360-3287-ND | NKK SWITCHES | M2011LL1W01 | 1 | 0 | 0 | 5 Weeks | SWITCH TOGGLE SPST 6A 125V |  | RoHS Compliant | Lead free | Unaffected Jun-2012
SPACER1,SPACER2,SPACER3,SPACER4 | 492-1072-ND | BIVAR INC | 9908-125 | 4 | 0 | 0 | 2 Weeks | ROUND SPACER #4 NYLON 1/8" |  | RoHS Compliant | Lead free | N/A
U1 | ATMEGA32A-PU-ND | ATMEL | ATMEGA32A-PU | 1 | 0 | 0 | 9 Weeks | IC MCU 8BIT 32KB FLASH 40DIP |  | RoHS Compliant | Lead free | Unaffected Jun-2013
U2 | 602-1285-ND | DIGI INTERNATIONAL | XBP24-Z7UIT-004J | 1 | 0 | 0 | 6 Weeks | XBEE PRO SET 50MW U.FL ANTENNA |  | RoHS Compliant | Lead free | Not Available
U3 | AP1117E33GDICT-ND | DIODES INCORPORATED (VA) | AP1117E33G-13 | 1 | 0 | 0 | 18 Weeks | IC REG LDO 3.3V 1A SOT223-3 | Alternate Packaging Exists | RoHS Compliant | Lead free | Unaffected Dec-2013
U5 | AP1117E50GDICT-ND | DIODES INCORPORATED (VA) | AP1117E50G-13 | 1 | 0 | 0 | 18 Weeks | IC REG LDO 5V 1A SOT223-3 | Alternate Packaging Exists | RoHS Compliant | Lead free | Unaffected Dec-2013
U6 | 67-1774-ND | LUMEX OPTO/COMPONENTS INC | LCM-S02004DSR | 1 | 0 | 0 | 10 Weeks | LCD MODULE 20X4 CHARACTER |  | RoHS Compliant | Lead free | Unaffected Jun-2013
U7,U8,U9 | 296-21995-1-ND | TEXAS INSTRUMENTS (VA) | TLC5917IDR | 3 | 0 | 0 | 7 Weeks | IC LED DRIVER LINEAR 16-SOIC | Alternate Packaging Exists | RoHS Compliant | Lead free | Unaffected Jun-2012
V1 | 732-2549-1-ND | WURTH ELECTRONICS INC (VA) | 82541110 | 1 | 0 | 0 | 8 Weeks | VARISTOR 18V 200A 1206 | Alternate Packaging Exists | RoHS Compliant | Lead free | Unaffected Sep-2011
X1 | XC569CT-ND | ECS INC (VA) | ECS-80-S-5P-TR | 1 | 0 | 0 | 10 Weeks | CRYSTAL 8MHZ SERIES SMD | Alternate Packaging Exists | RoHS non-compliant | Contains lead | Unaffected Jun-2011

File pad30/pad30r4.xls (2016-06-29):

Reference | Quantity | Name | Description | Package | Digi-Key Part | Value | V_Max | I_Max | R_Max | V_Max_AC | I_Max_AC | Manufacturer | Manufacturer Part | Newark Part | Mouser Part | Cost | R_Off | R_On | T_Trip | Temp_Nom | Other
C10,C11,C12,C8,C9 | 5 | 0.1uf | Capacitor | C1206 | 311-1435-1-ND | 0.1uf
R13,R14,R5,R8 | 4 | 1.0M | Small Resistor | R1206 | 311-1.00MFRCT-ND
C3,C6 | 2 | 10 mfd | Small Electrolytic | C1206 | 311-1466-1-ND
C5 | 1 | 100 mfd | Small Electrolytic | eeehae101 | PCE4705CT-ND
J16 | 1 | 16 pin dip socket | SOCKET IC OPEN FRAME 16POS .3" | package name for PCB layout | 3M5463-ND
R15,R16,R17,R18 | 4 | 1K | Small Resistor | R1206 | 311-1.00KFRCT-ND
A1 | 1 | 2.4Ghz Antenna | ANTENNA 2.45GHZ 7" RA U.FL PLUG | .. | 0600-00039-ND
C1,C2 | 2 | 20pf | Capacitor | C1206 | 311-1153-1-ND | 20pf
R1,R3,R6,R9 | 4 | 301K | Small Resistor | R1206 | 311-301KFRCT-ND
R10,R2,R4,R7 | 4 | 56.2K | Small Resistor | R1206 | 311-56.2KFRCT-ND
X1 | 1 | 8 Mhz | Crystal | csm-7 | XC569CT-ND
C7 | 1 | 8.2pf | Capacitor | C1206 | 311-1222-1-ND | 8.2pf
U2 | 1 | ATMega32A | ATMega32A | 40DIP600 | ATMEGA32A-PU-ND
U5 | 1 | AZ1117-33 | LD1117S33 | WSOT-223 | AZ1117H-3.3TRE1DICT-ND
B1 | 1 | BUZZER | Buzzer | 458-1092-ND | 458-1088-ND |  |  |  |  |  |  |  |  | .. | .. | ..
Banana Jack 1,Banana Jack 2,Banana Jack 3 | 3 | Banana Jack | CONN JACK BANANA INSUL NYLON BLA | package name for PCB layout | J152-ND
Banana Jack 4,Banana Jack 5,Banana Jack 6 | 3 | Banana Jack | CONN JACK BANANA INSUL NYLON RED | package name for PCB layout | J151-ND
D1 | 1 | Bridge | Bridge | 4-SMD | 641-1344-5-ND
cap1,cap2 | 2 | CAP TACTILE ROUND BLACK | CAP TACTILE ROUND BLACK | package name for PCB layout | 679-2172-ND
S1,S2 | 2 | Continuity | Single Pole Push Switch | 3ESH9-15.0 | 679-2226-ND
SE1,SE2 | 2 | EXTENDER SWITCH 7MM | EXTENDER SWITCH 7MM HEIGHT | package name for PCB layout | 679-2203-ND
E1 | 1 | Enclosure | BOX 5.62X3.25X2.50 ALMOND | .. | SR153A-ND
j15 | 1 | IC Socket DIP 40 pin | SOCKET IC OPEN FRAME 40POS .6" | package name for PCB layout | 3M5471-ND |  |  |  |  |  |  |  |  |  |  |  |  |  |  |  | ..
J3 | 1 | JTAG | 5X2HDR-100 | 5X2HDR-50 | S9013E-05-ND
LP1,LP2 | 2 | LIGHT PIPE .250" ROUND PNL MT | LIGHT PIPE .250" ROUND PNL MT |  | 492-1142-ND
QD1,QD2,QD3,QD4,QD5,QD6 | 6 | Quick Disc Female Connector | Quick Disconnect 0.205 x 0.250 x 0.020 | package name for PCB layout | A0903-ND
J17,J18 | 2 | Quick Disconnect Female | TERM PC QF .205" VERT .205X.020" | package name for PCB layout | 3525K-ND
J1,J2,J5,J6,J7,J8 | 6 | Quick-Connect | Contact in | Amp63650 | 1287K-ND
F1 | 1 | RELAY-THERMISCH-NC | Relay thermisch NC | AutoBreaker2 | 302-1242-ND
K1,K2,K3,K4 | 4 | Relay | RELAY AUTOMOTIVE SPDT 30A 12V | .. | PB679-ND
J10,J11,J12,J9 | 4 | Relay | Relay SPST-NO | VCF4-1000 | PB232-ND
D2,D3 | 2 | SMP4-SRGY | SMP4-SRGY | PLCC-4 | 492-1227-1-ND
J4 | 1 | TestPoint | Header 1x3 | 1X3HDR-100 | 609-3470-ND
U3 | 1 | ULN2003A | Driver | 16DIP300 | 296-1979-5-ND
V1,V2,V3 | 3 | Varistor | Varistor | C1206 | 732-2549-1-ND |  | .. |  |  |  |  |  | .. | .. | .. | .. | .. | .. | .. | ..
U1 | 1 | XBee-pro s2c | XBee | XBee | 602-1563-ND
J13,J14 | 2 | Xbee Header | CONN RECEPT 2MM SINGLE STR 10POS | .. | S5751-10-ND

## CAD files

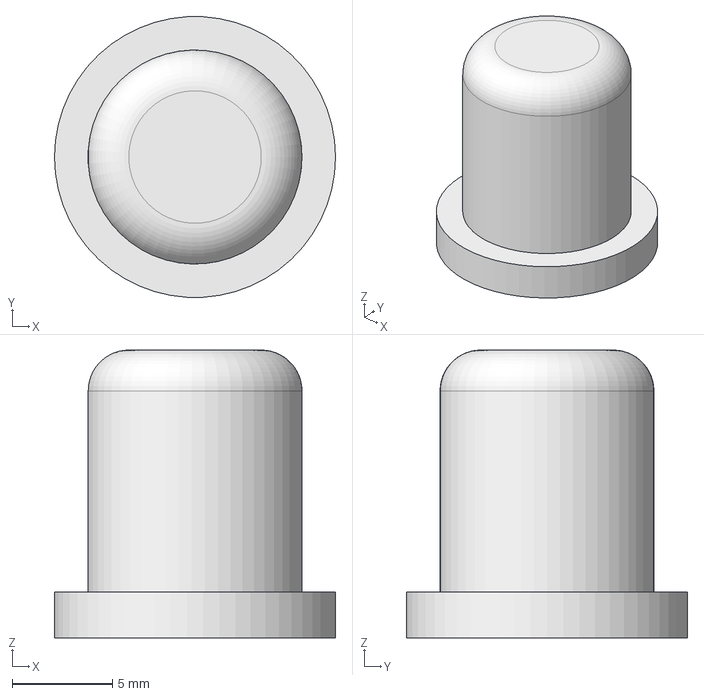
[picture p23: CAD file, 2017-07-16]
3FS_cap.FCStd
14.0 x 14.0 x 14.4 mm

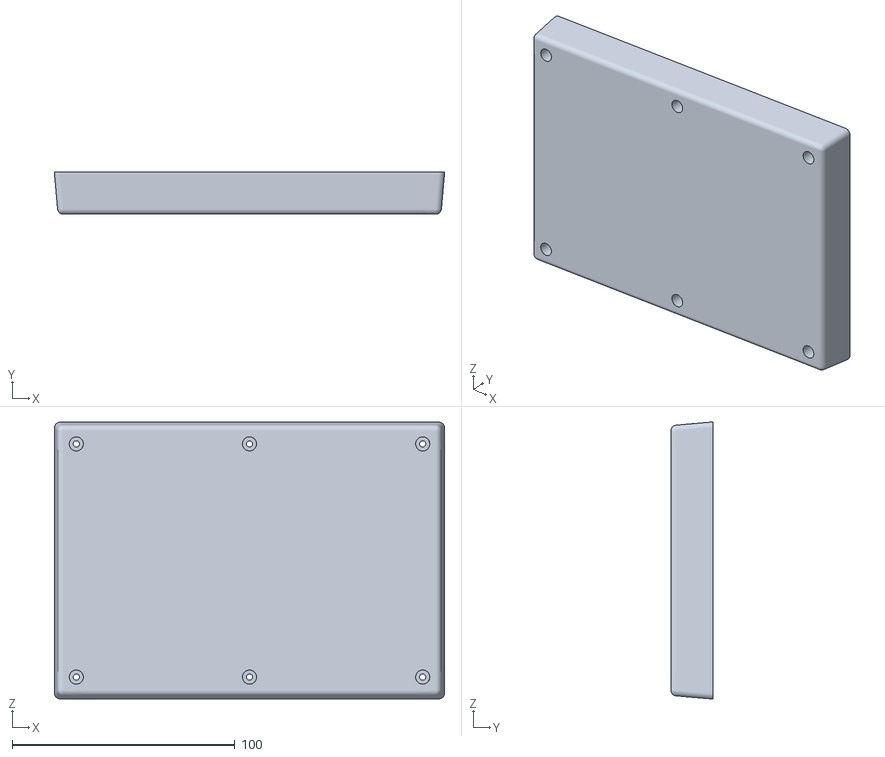
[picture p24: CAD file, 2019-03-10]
controller30/17s-bottom v7.stl
175.0 x 18.9 x 124.2

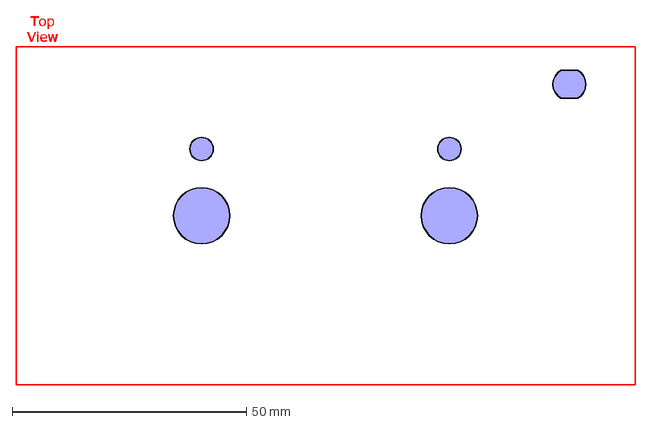
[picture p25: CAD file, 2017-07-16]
pad30/pad-panel.dxf
Top View

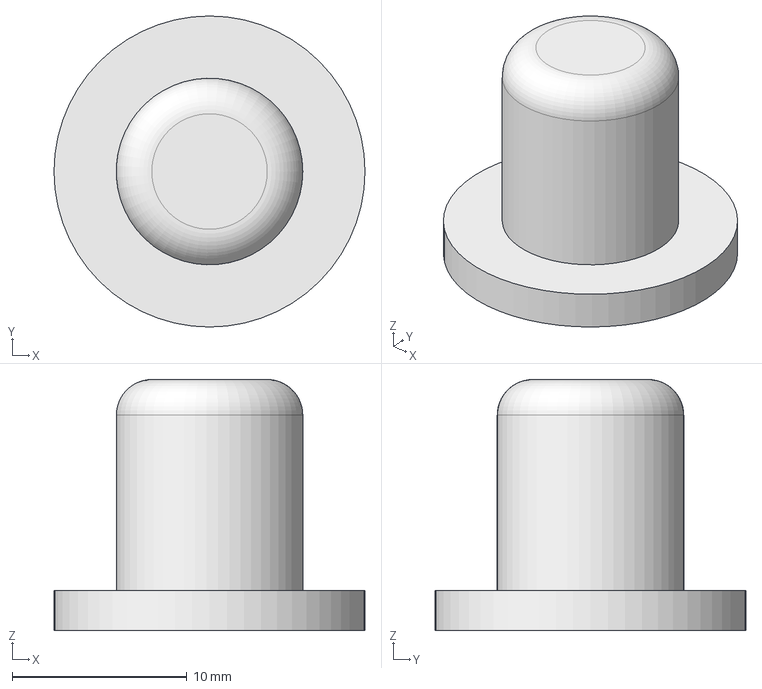
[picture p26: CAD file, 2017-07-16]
3FS_cap-2.FCStd
17.8 x 17.8 x 14.4 mm

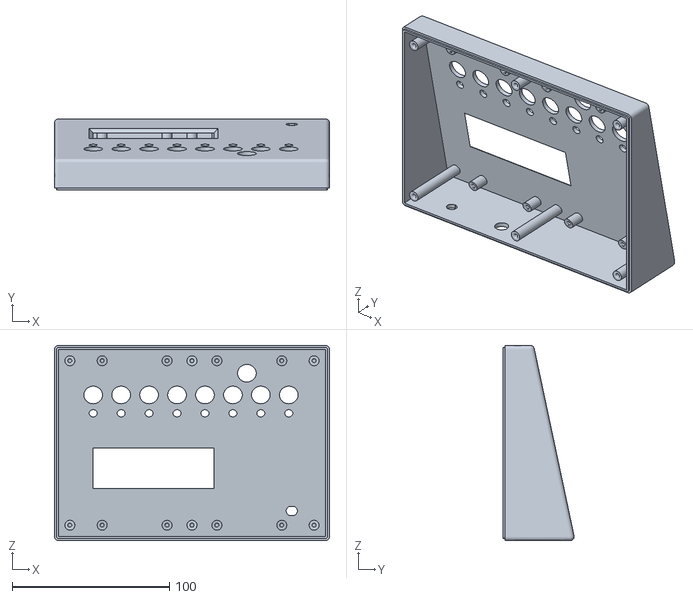
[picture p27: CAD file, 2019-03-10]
controller30/17S-controller mod v25.stl
175.0 x 45.4 x 124.2

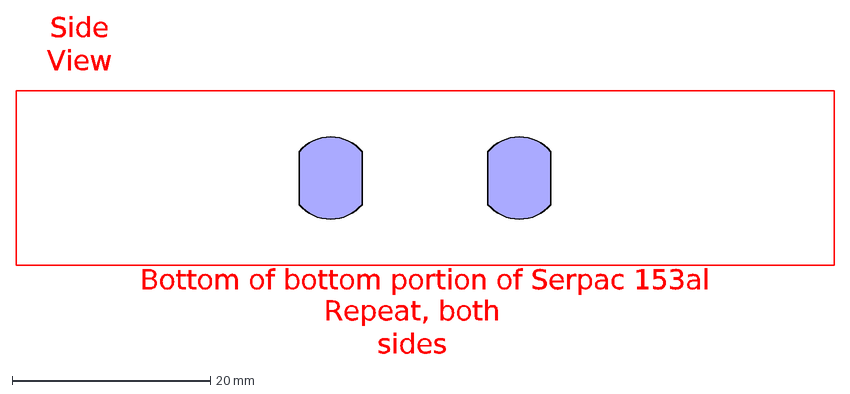
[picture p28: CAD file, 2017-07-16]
pad30/pad-side-panel.dxf
Repeat, both sides
Side View
Bottom of bottom portion of Serpac 153al

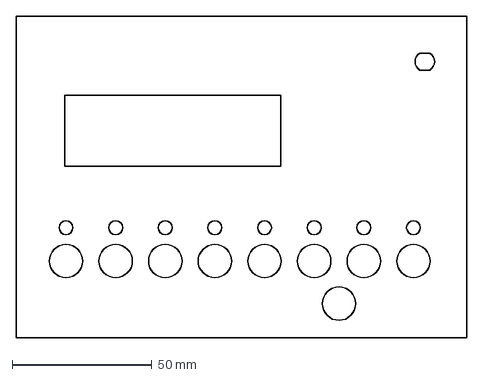
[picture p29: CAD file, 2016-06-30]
controller30/panel-cref.dxf
161.3 x 115.1 mm

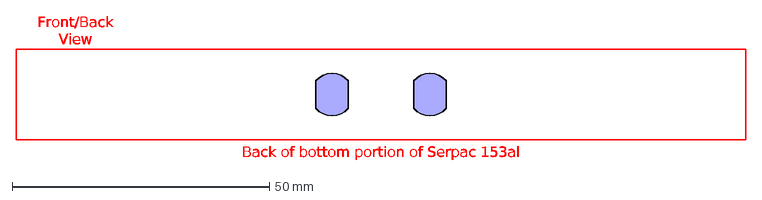
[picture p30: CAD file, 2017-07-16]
pad30/pad-back-panel.dxf
Back of bottom portion of Serpac 153al
Front/Back View

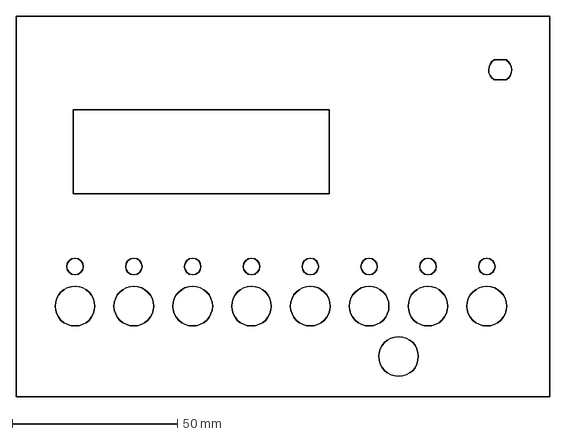
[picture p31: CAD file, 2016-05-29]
controller30/panel.dxf
161.3 x 115.1 mm

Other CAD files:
3FS_cap-2.stl
3FS_cap.stl
controller30/17S-controller mod v25.f3d
controller30/17s-bottom v7.f3d
controller30/controller-bottom.f3d
controller30/controller-top.f3d

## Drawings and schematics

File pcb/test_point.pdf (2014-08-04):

## TP-2S-S

## TP-2S-M

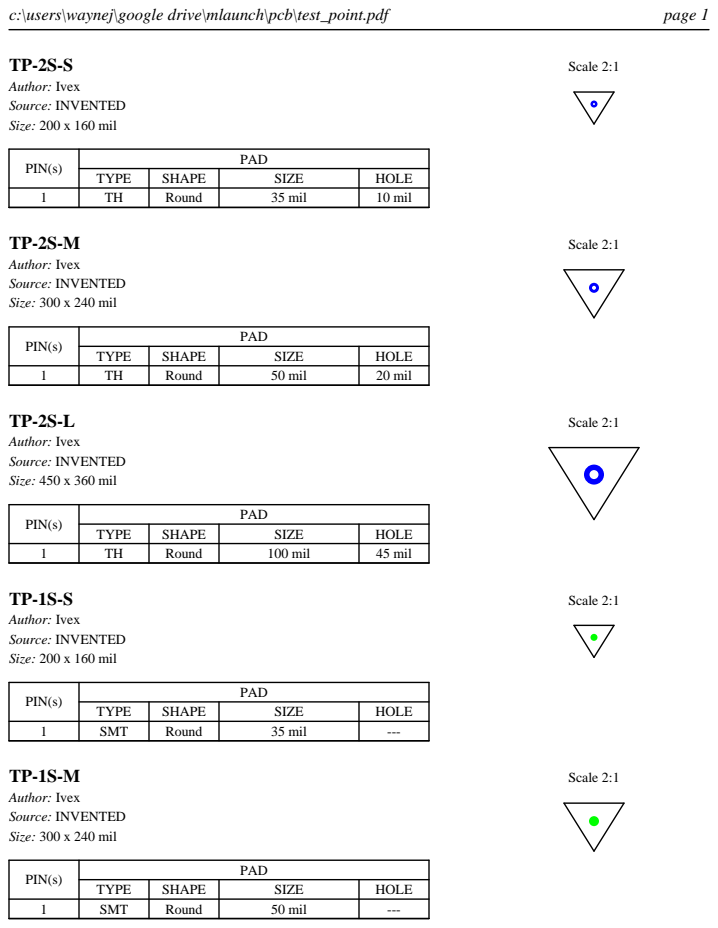
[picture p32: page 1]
c:\users\waynej\google drive\mlaunch\pcb\test_point.pdf; page 1; Author: Ivex Source: INVENTED Size: 200 x 160 mil; Scale 2:1; Author: Ivex Source: INVENTED Size: 300 x 240 mil; Author: Ivex Source: INVENTED Size: 450 x 360 mil

PIN(s) | PAD

TYPE | SHAPE | SIZE | HOLE

1 | TH | Round | 35 mil | 10 mil

1 | TH | Round | 50 mil | 20 mil

1 | TH | Round | 100 mil | 45 mil

1 | SMT | Round | 35 mil | ---

1 | SMT | Round | 50 mil | ---

c:\users\waynej\google drive\mlaunch\pcb\test_point.pdf | page 2

## TP-1S-L

Author: Ivex
Source: INVENTED
Size: 450 x 360 mil
PIN(s) | PAD
TYPE | SHAPE | SIZE | HOLE
1 | SMT | Round | 100 mil | ---

Scale 2:1

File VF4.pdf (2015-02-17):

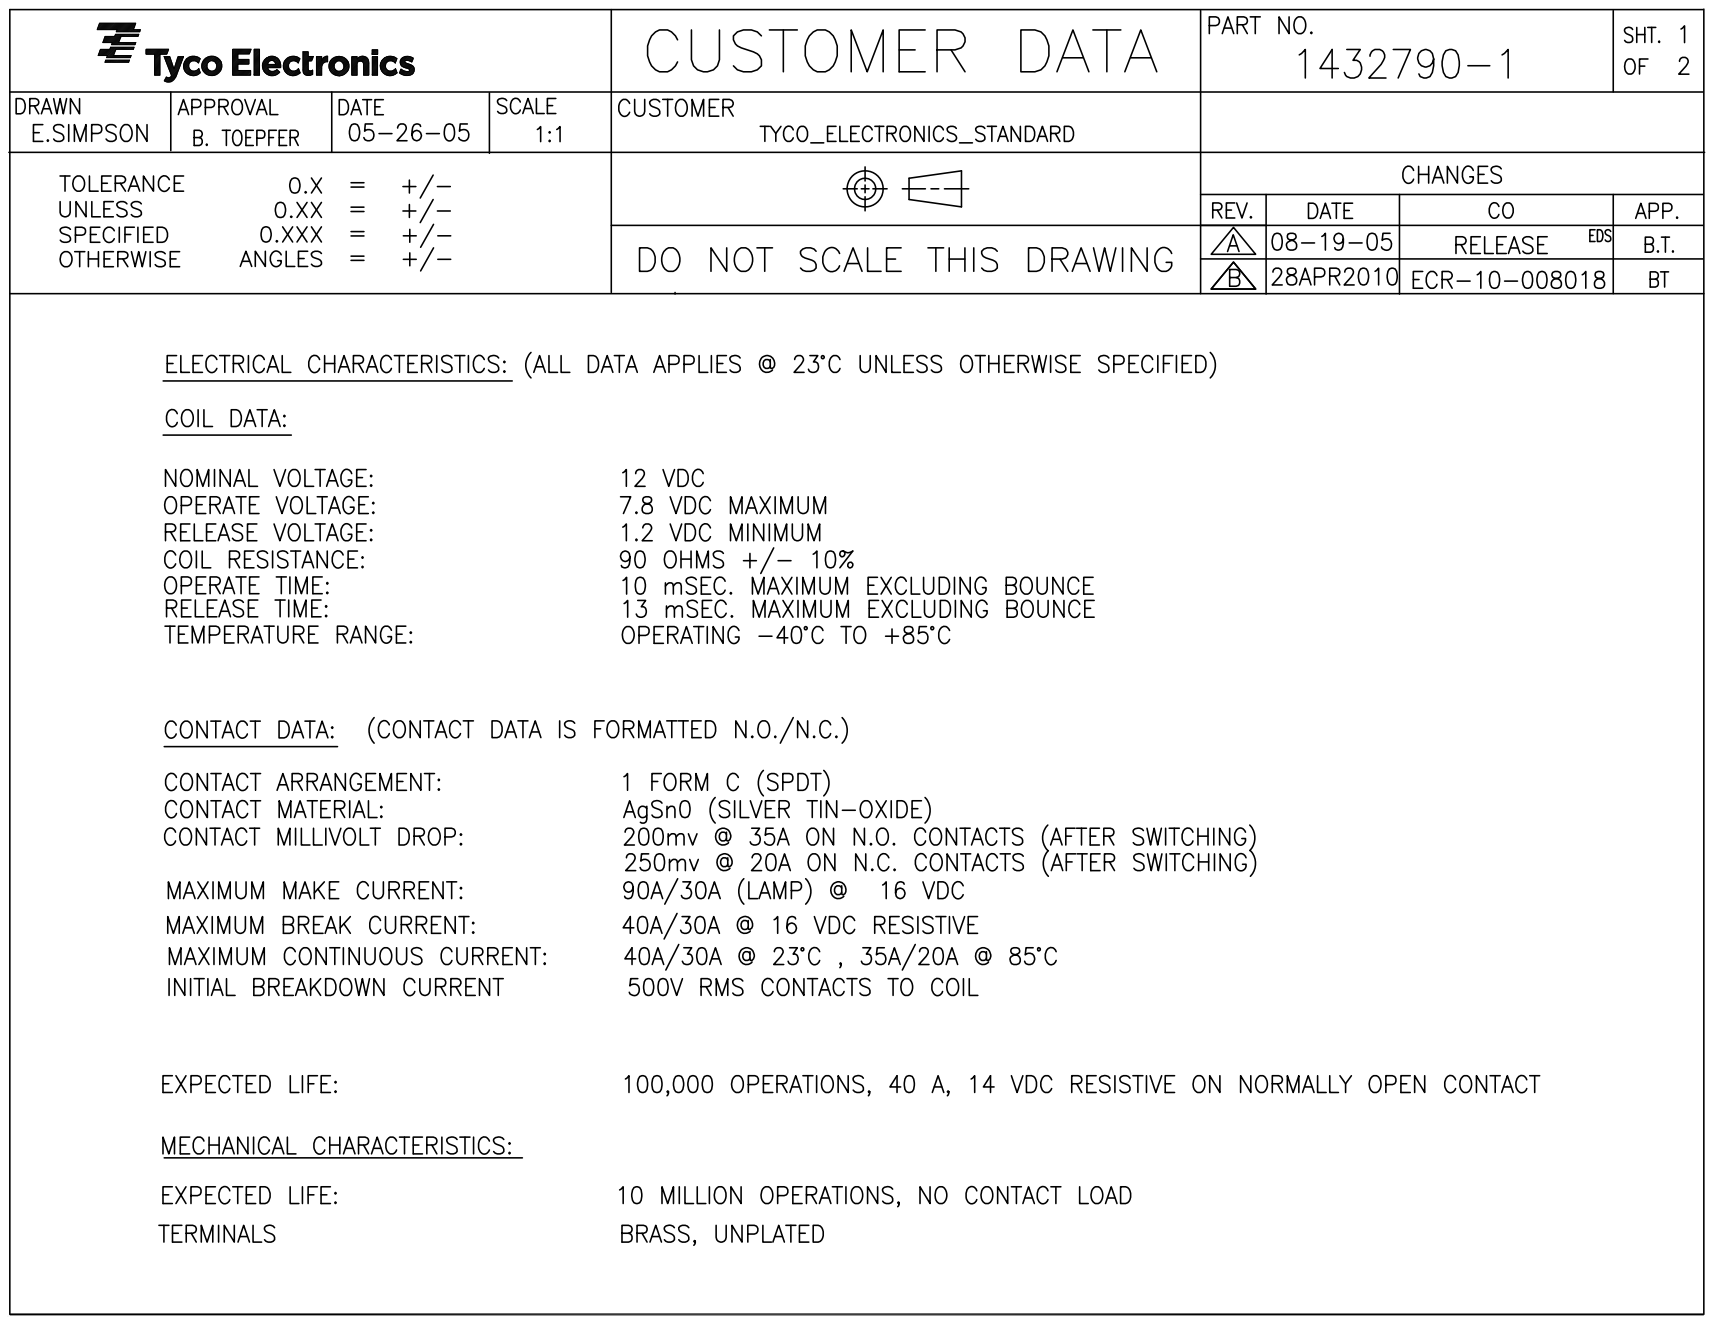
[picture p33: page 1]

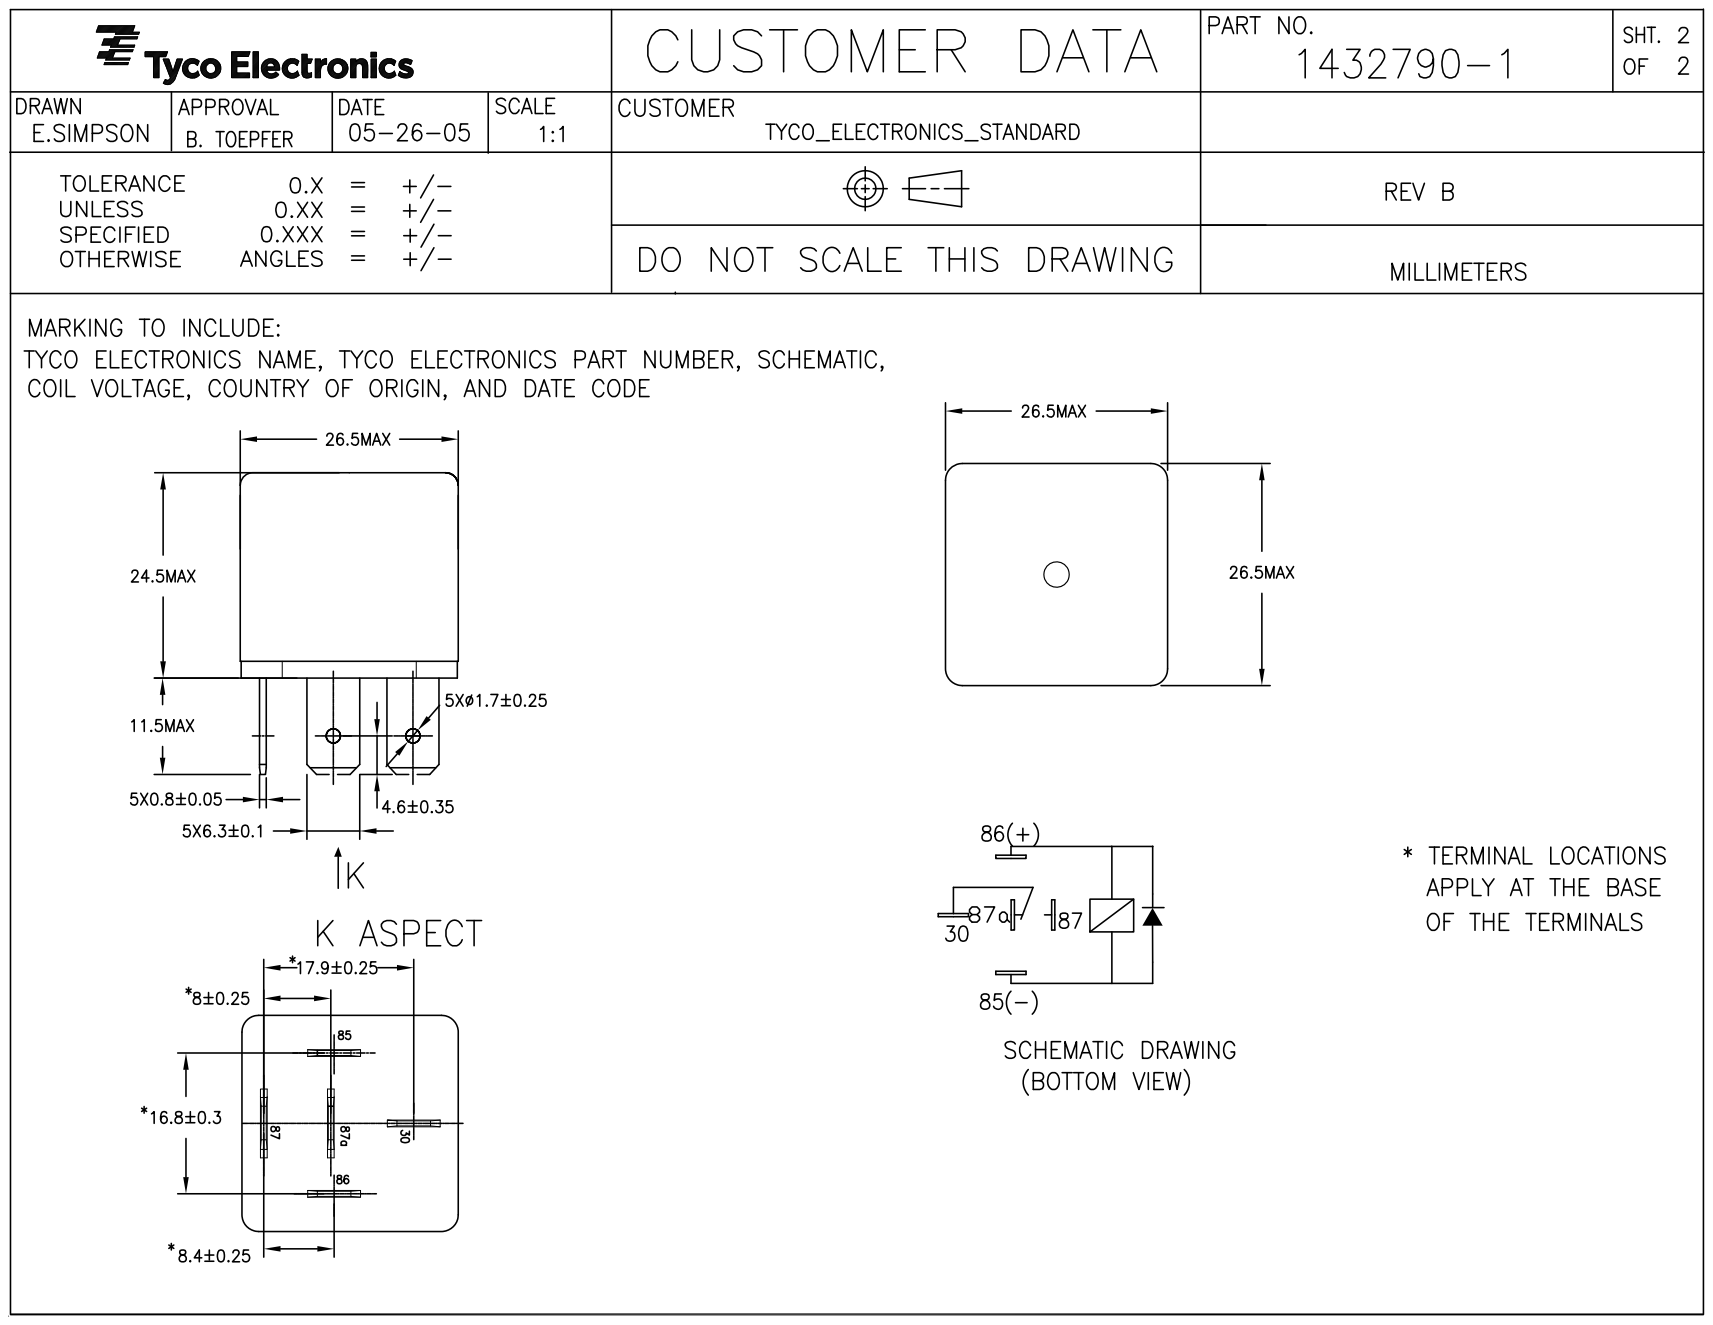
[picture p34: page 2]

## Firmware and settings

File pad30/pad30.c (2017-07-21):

/*
 * software.c
 *
 * Created: 2/16/2014 10:44:30 AM
 *  Author: waynej
 */

#include "pad30.h"
#include "../common/config.h"

#include <avr/io.h>
#include <avr/interrupt.h>
#include <avr/cpufunc.h>
#include <util/delay.h>
#include <avr/eeprom.h>
#include <string.h> 

#include "../common/adc.h"
#include "../common/uart.h"
#include "../common/zb.h"
#include "../common/Timer0.h"

#include "launchFSM.h"
#include "switchFSM.h"
#include "statusFSM.h"
#include "linkFSM.h"

FILE xbee = FDEV_SETUP_STREAM(uart_putchar, uart_getchar, _FDEV_SETUP_RW);

char txBuffer[80] =
    { 0xff, 0xff, 0xff, 0xff, 0xff, 0xff, 0xff, 0xff, 0xff, 0xff, 0xff, 0xff,
            0xff, 0xff, 0xff, 0xff, 0xff, 0xff, 0xff, 0xff, 0xff, 0xff, 0xff,
            0xff, 0xff, 0xff, 0xff, 0xff, 0xff, 0xff, 0xff, 0xff, 0xff, 0xff,
            0xff, 0xff, 0xff, 0xff, 0xff, 0xff, 0xff, 0xff, 0xff, 0xff, 0xff,
            0xff, 0xff, 0xff, 0xff, 0xff, 0xff, 0xff, 0xff, 0xff, 0xff, 0xff,
            0xff, 0xff, 0xff, 0xff, 0xff, 0xff, 0xff, 0xff, 0xff, 0xff, 0xff,
            0xff, 0xff, 0xff, 0xff, 0xff, 0xff, 0xff, 0xff, 0xff, 0xff, 0xff,
            0xff, 0xff };

zbAddr controllerAddress =
    {
        { 0, 0, 0, 0, 0, 0, 0xff, 0xff } };
zbNetAddr controllerNAD =
    {
        { 0xff, 0xfe } };

struct padStruct pads[2] =
    {
        { IDLE,
        Enable1,
        Launch1,
        Green1,
        Red1 },
        { IDLE,
        Enable2,
        Launch2,
        Green2,
        Red2 } };

unsigned int adc0hist[10];
unsigned int adc1hist[10];
unsigned int adc2hist[10];
unsigned int adc3hist[10];

volatile unsigned int histTimer = 1000 / TIMER0_PERIOD;

volatile unsigned long vBatt;

bool ident = false;
int identTimer;
int histptr = 0;

struct epromStruct EEMEM eprom;

#define noTRACE
#if defined(TRACE)
unsigned char trace_buffer[256];
unsigned char *trace_buffer_ptr=trace_buffer;
unsigned char *trace_buffer_end=trace_buffer+sizeof trace_buffer-1;
#endif

void init();
void rxc(void);
void rxData(zbRx* rxPkt);
void rxPkt(unsigned char *data, unsigned int length);
void zbWrite(void *buff, unsigned int count);
void timer0(void);
void initFlash();
void handleEnable(zbRx* rxPkt, zbAddr addr, zbNetAddr nad);
void handleReset(zbRx* rxPkt);
void handleLaunch(zbRx* rxPkt);
void handleUnlaunch(zbRx* rxPkt);
void handleAssign(zbRx* rxPkt);
void handleIdent(zbRx* rxPkt);

int main(void)
{
    bool sw1pressed = false, sw2pressed = false;
    long adc0, adc1, adc2, adc3;

    init();

    setRed1()
    ;
    setRed2()
    ;

    char nodeName[] = "PADxx";
    nodeName[3] = pads[0].padAssign;
    nodeName[4] = pads[1].padAssign;

    linkFSMinit(nodeName);

    resetRed1()
    ;
    resetRed2()
    ;

    while (1)
    {
        linkFSMToDo();

        /*
         *  Converting from the ADC value to a voltage is pretty complicated.  There
         *  is a diode bridge that biases ground by about .8 volts and then
         *  the level shift created by the resistor matrix.  To solve this I took
         *  some empirical readings and constructed a graph.  The trendline for the
         *  graph of these values came out with a slope of 55.583 V/bit with an x
         *  intercept of 14.44.  The following reconstructs the voltage (in
         *  hundredths of a volt so we don't need floating point).
         */

        adc2 = (long) adc_value(2);
        adc3 = (long) adc_value(3);
        if (adc2 > adc3)
        {
            vBatt = (((long) adc2) - 16) * 100000 / 59571;
        } else
        {
            vBatt = (((long) adc3) - 16) * 100000 / 59571;
        }

        if (vBatt < 0)
        {
            vBatt = 0;
        }

        long r;
        if (pads[0].launchState == PAD_ENABLED
                || pads[0].launchState == SW_ENABLED)
        {
            adc0 = (long) adc_value(0);
            if (adc2 > adc3)
            {
                long rCd = ((long) adc0) * 148;
                long rBatt = ((long) adc2) * 7;
                r = (rCd - rBatt + 3798) / 100;
            } else
            {
                long rCd = ((long) adc0) * 147;
                long rBatt = ((long) adc2) * 140;
                r = (rBatt - rCd + 5386) / 100;
            }

            if (r < 0)
            {
                r = 0;
            }

            if (r > 50000)
            {
                pads[0].contResistance = -1;
            } else
            {
                pads[0].contResistance = r;
            }
            pads[0].contValid = true;
        }

        if (pads[1].launchState == PAD_ENABLED
                || pads[1].launchState == SW_ENABLED)
        {
            adc1 = (long) adc_value(1);
            if (adc2 > adc3)
            {
                long rCd = ((long) adc1) * 148;
                long rBatt = ((long) adc2) * 7;
                r = (rCd - rBatt + 3798) / 100;
            } else
            {
                long rCd = ((long) adc1) * 147;
                long rBatt = ((long) adc2) * 140;
                r = (rBatt - rCd + 5386) / 100;
            }

            if (r < 0)
            {
                r = 0;
            }

            if (r > 50000)
            {
                pads[1].contResistance = -1;
            } else
            {
                pads[1].contResistance = r;
            }
            pads[1].contValid = true;
        }

        if (!sw1pressed && isClosed(0))
        {	// sw1 has transitioned from open to closed
            SWEnable(0);
            sw1pressed = true;
        }

        if (sw1pressed && !isClosed(0))
        {	// sw1 has transitioned from closed to open
            SWReset(0);
            sw1pressed = false;
        }

        if (!sw2pressed && isClosed(1))
        {	// sw2 has transitioned from open to closed
            SWEnable(1);
            sw2pressed = true;
        }

        if (sw2pressed && !isClosed(1))
        {	// sw2 has transitioned from closed to open
            SWReset(1);
            sw2pressed = false;
        }

        if (histTimer == 0)
        {
            memmove(&adc0hist[1], &adc0hist[0],
                    sizeof(adc0hist) - sizeof(adc0hist[0]));
            adc0hist[0] = adc_value(0);

            memmove(&adc1hist[1], &adc1hist[0],
                    sizeof(adc1hist) - sizeof(adc1hist[0]));
            adc1hist[0] = adc_value(1);

            memmove(&adc2hist[1], &adc2hist[0],
                    sizeof(adc2hist) - sizeof(adc2hist[0]));
            adc2hist[0] = adc_value(2);

            memmove(&adc3hist[1], &adc3hist[0],
                    sizeof(adc3hist) - sizeof(adc3hist[0]));
            adc3hist[0] = adc_value(3);

            histTimer = 1000 / TIMER0_PERIOD;
        }
    }
}

void init()
{
    unsigned char init[4];

    DDRA = _BV(Launch1) | _BV(Enable1) | _BV(Launch2) | _BV(Enable2);// PA4-7 output
    DDRB = _BV(Red1) | _BV(Green1) | _BV(Siren) | _BV(Red2) | _BV(Green2);// PB0-1, 3-5 are output
    PORTB = _BV(ContSW1) | _BV(ContSW2);			// Set pullup on switches

    DDRD |= _BV(7);

    if (!(PINB & _BV(ContSW1)) || !(PINB & _BV(ContSW2)))
    {
        _delay_ms(100);
        if (!(PINB & _BV(ContSW1)) || !(PINB & _BV(ContSW2)))
        {
            eeprom_write_byte(&eprom.init[0], 0);
        }
    }

    eeprom_read_block(init, &eprom.init[0], sizeof init);

    if (init[0] == 'I' && init[1] == 'n' && init[2] == 'i' && init[3] == 't')
    {
        // Read configured pad assignments
        pads[0].padAssign = eeprom_read_byte(&eprom.padAssign[0]);
        pads[1].padAssign = eeprom_read_byte(&eprom.padAssign[1]);
    }

    timer0_init(CS_1024, timer0);				// Timer uses system clock/1024
    timer0_set(F_CPU / 1024 / 1000 * TIMER0_PERIOD);

    uart_txBuff(txBuffer, sizeof txBuffer);

    uart_init(UART_BAUD, rxc);

    adc_init(0, ADMUX_REF_INT | ADMUX_AD0);
    adc_init(1, ADMUX_REF_INT | ADMUX_AD1);
    adc_init(2, ADMUX_REF_INT | ADMUX_AD2);
    adc_init(3, ADMUX_REF_INT | ADMUX_AD3);
    adc_init(4, ADMUX_REF_INT | ADMUX_122);
    adc_init(5, ADMUX_REF_INT | ADMUX_GND);

    adc_run();

    zbInit(&zbWrite, &rxPkt);

    sei();								// enable interrupts

    // Wait till we've completed the initial voltage checks.
    while (!adc_valid(0) && !adc_valid(1) && !adc_valid(2) && !adc_valid(3))
    {
    }
}

/* Timer 0 interrupt */
void timer0(void)
{
    linkFSMtimer();

    timer0_set(F_CPU / 1024 / 1000 * TIMER0_PERIOD);

    if (ident)
    {
        identTimer++;
        identTimer %= 100 / TIMER0_PERIOD;
        if (identTimer == 0 / TIMER0_PERIOD)
        {
            setRed1()
            ;
            setGreen1()
            ;
            setRed2()
            ;
            setGreen2()
            ;
        } else if (identTimer == 50 / TIMER0_PERIOD)
        {
            resetRed1()
            ;
            resetGreen1()
            ;
            resetRed2()
            ;
            resetGreen2()
            ;
        }
    } else
    {
        switchFSMtimer();

        padFSMtimer(0);
        padFSMtimer(1);

        statusFSMtimer();
    }

    if (histTimer > 0)
        histTimer--;
}

/* Flash the lights twice at initialization */
void initFlash()
{
    setRed1()
    ;
    setGreen1()
    ;
    setRed2()
    ;
    setGreen2()
    ;
    _delay_ms(100);
    resetRed1()
    ;
    resetGreen1()
    ;
    resetRed2()
    ;
    resetGreen2()
    ;
    _delay_ms(100);
    setRed1()
    ;
    setGreen1()
    ;
    setRed2()
    ;
    setGreen2()
    ;
    _delay_ms(100);
    resetRed1()
    ;
    resetGreen1()
    ;
    resetRed2()
    ;
    resetGreen2()
    ;
}

/* Receive a single character from the UART */
void rxc(void)
{
    unsigned char ch = UDR;

#if defined(TRACE)
    *(trace_buffer_ptr++)=ch;
    if (trace_buffer_ptr==trace_buffer_end)
    {
        trace_buffer_ptr=trace_buffer;
    }
#endif

    zbReceivedChar(ch);
}

/* Write a buffer of data to XBee */
void zbWrite(void *buff, unsigned int count)
{
    fwrite(buff, count, 1, &xbee);
}

/* Handle received XBee packet */
void rxPkt(unsigned char *data, unsigned int length)
{
    zbPkt *pkt = (zbPkt *) data;
    switch (pkt->frameType)
    {
    case ZB_RECEIVE_PACKET:
        rxData(&pkt->zbRX);
        break;

    default:
        linkFSMpkt(pkt);
        break;
    }
}

/* Handle received XBee Data */
void rxData(zbRx* rxPkt)
{
    switch (rxPkt->data[0])
    {
    case 'E':
        handleEnable(rxPkt, rxPkt->dest, rxPkt->nad);
        break;
    case 'R':
        handleReset(rxPkt);
        break;
    case 'L':
        handleLaunch(rxPkt);
        break;
    case 'U':
        handleUnlaunch(rxPkt);
        break;
    case 'A':
        handleAssign(rxPkt);
        break;
    case 'I':
        handleIdent(rxPkt);
        break;
    }
}

void handleEnable(zbRx* rxPkt, zbAddr addr, zbNetAddr nad)
{
    controllerAddress = addr;
    controllerNAD = nad;

    for (int i = 0; i < PAD_COUNT; ++i)
    {
        if (rxPkt->data[1] == pads[i].padAssign)
        {
            padEnable(i);
        }
    }
}

void handleReset(zbRx* rxPkt)
{
    for (int i = 0; i < PAD_COUNT; ++i)
    {
        if (rxPkt->data[1] == pads[i].padAssign)
        {
            padReset(i);
        }
    }
}

void handleLaunch(zbRx* rxPkt)
{
    for (int i = 0; i < PAD_COUNT; ++i)
    {
        if (rxPkt->data[1] == pads[i].padAssign)
        {
            padLaunch(i);
        }
    }
}

void handleUnlaunch(zbRx* rxPkt)
{
    for (int i = 0; i < PAD_COUNT; ++i)
    {
        if (rxPkt->data[1] == pads[i].padAssign)
        {
            padUnlaunch(i);
        }
    }
}

void handleAssign(zbRx* rxPkt)
{
    ident = false;

    unsigned char pad0 = rxPkt->data[1];
    unsigned char pad1 = rxPkt->data[2];

    pads[0].padAssign = pad0;
    pads[1].padAssign = pad1;

    eeprom_write_block("Init", &eprom.init, 4);
    eeprom_write_byte(&eprom.padAssign[0], pad0);
    eeprom_write_byte(&eprom.padAssign[1], pad1);

    char nodeName[] = "PADxx";
    nodeName[3] = pad0;
    nodeName[4] = pad1;

    zb_ni(0, nodeName);

    resetRed1()
    ;
    resetGreen1()
    ;
    resetRed2()
    ;
    resetGreen2()
    ;
}

void handleIdent(zbRx* rxPkt)
{
    ident = true;
}

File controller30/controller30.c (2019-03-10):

/*
 * controller30.c
 *
 * Created: 2/26/2014 7:34:55 PM
 *  Author: waynej
 */ 


#include "controller30.h"
#include "../common/config.h"

#include <avr/io.h>
#include <avr/interrupt.h>
#include <util/delay.h>
#include <avr/eeprom.h>
#include <string.h>

#include "../common/led.h"
#include "../common/OLED.h"
#include "../common/adc.h"
#include "../common/uart.h"
#include "../common/zb.h"
#include "../common/Timer0.h"
#include "../common/Timer1.h"
#include "linkFSM.h"
#include "switchFSM.h"

void init(void);
int zbWrite(void *buff, unsigned int count);
void timer0(void);
void enable(int sw);
void disable(int sw);
void padFSMTimer(void);
void sendEnable( int sw );
void sendDisable( int sw );
void sendLaunch( int sw );
void sendIdent( zbAddr addr, zbNetAddr netAddr );
void sendAssign( int sw );

FILE xbee = FDEV_SETUP_STREAM(uart_putchar, uart_getchar, _FDEV_SETUP_RW);

char rxBuffer[200]="";
char txBuffer[200]="";

unsigned int greenLeds=0;
unsigned int redLeds=0;
unsigned int yellowLeds=0;

volatile struct padInfo pads[]=
{
    {
        IDLE,
        '1'
    },
    {
        IDLE,
        '2'
    },
    {
        IDLE,
        '3'
    },
    {
        IDLE,
        '4'
    },
    {
        IDLE,
        '5'
    },
    {
        IDLE,
        '6'
    },
    {
        IDLE,
        '7'
    },
    {
        IDLE,
        '8'
    }
};

struct NewPad newPad[8];

/* Flag to force manual initialization */
bool notInitialized=false;

/**
 * mLaunch controller main
 *
 * We get control here as soon as Atmel runtime is initialized.  It initializes 
 * the platform, then loops, looking for work to do.
 */
int main(void)
{
    bool launchPressed=false;
   
    
    init();

    LED_output(0x0, 0x0, 0x0);            /* Turn off LEDs */

    OLED_display(true, false, false);    /* Display on, Cursor off, Blink off */
    OLED_functionSet(true, 0);            /* 8 bit, English/Japanese char set */
    OLED_entryModeSet(true, false);        /* Increment, no shift */
    OLED_cursorDisplayShift(false, true); /* Shift cursor, Right */

    OLED_clearDisplay();                /* Blank display */

    OLED_XYprintf(0, 0, "mLaunch 3.1");
    OLED_XYprintf(0, 0, __DATE__);
    OLED_XYprintf(0, 2, "Copyright 2017 by");
    OLED_XYprintf(0, 3, "Wayne Johnson");

    OLED_clearLine(2);
    OLED_clearLine(3);
    
#if defined(iDEBUG)
        notInitialized=true;
#else
    if (PINB!=0xFF)
    {
        notInitialized=true;
        OLED_XYprintf(0, 3, "Reinitializing");
    }
#endif

    OLED_XYprintf(0, 1, "Comm Init");
    OLED_clearEOL();

    /* Flash the pad lights to be pretty */
    for(int i=0; i<10; ++i)
    {
        unsigned int bit=1<<i;
        LED_output(bit, bit>>1, bit>>2);
        _delay_ms(100);
        LED_output(0x0, 0x0, 0x0);
    }

    linkInit(notInitialized);

    // Leave the copyright on a bit longer  
    OLED_clearLine(1);
    OLED_clearLine(2);
    OLED_clearLine(3);
    
    /* main loop */
    bool displayCluttered=false;
    while(1)
    {
        bool allOpen=true;
        
        linkFSM();
        
        if (isLinkReady())
        {
        
            for(int sw=0; sw<8; ++sw)
            {
                if(!pads[sw].discovered)
                {
                    continue;
                }
            
                if (isClosed(sw))
                {
                    allOpen=false;
                    if (pads[sw].padState == IDLE)
                    {
                        enable(sw);
                    } 
                    else if (pads[sw].padState == ENABLED)
                    {
                        disable(sw);
                    }
                }
                else
                {
                    if (pads[sw].padState == PRESSED2ENABLE)
                    {
                        pads[sw].padState=ENABLED;
                    } 
                    else if (pads[sw].padState == PRESSED2DISABLE)
                    {
                        pads[sw].padState=IDLE;
                    }
                }
            
                if (pads[sw].newStatus)
                {
                    if (pads[sw].padState == PRESSED2ENABLE)
                    {
                        OLED_clearDisplay();
                        OLED_XYprintf(0,0, "Pad %d", sw+1);
                        if (pads[sw].contResistance==-1)
                        {
                            OLED_XYprintf(0,1, "Resistance=OPEN", pads[sw].contResistance);
                        }
                        else
                        {
                            OLED_XYprintf(0,1, "Resistance=%d", pads[sw].contResistance);
                        }

                        OLED_XYprintf(0,2, "Batt=%d.%d", pads[sw].batt/100, pads[sw].batt%100);
                        displayCluttered=true;
                        pads[sw].newStatus=false;
                    }
                }
            
                if (pads[sw].padState == ENABLED ||
                    pads[sw].padState == PRESSED2ENABLE)
                {
                    if (pads[sw].statusValid)
                    {
                        if (pads[sw].contState==0)
                        {
                            redLeds|=_BV(sw);
                            greenLeds&=~_BV(sw);
                            yellowLeds&=~_BV(sw);
                        }
                        else
                        {
                            redLeds&=~_BV(sw);
                            greenLeds|=_BV(sw);
                            yellowLeds&=~_BV(sw);
                        }
                    }
                    else
                    {
                        redLeds&=~_BV(sw);
                        greenLeds&=~_BV(sw);
                        yellowLeds|=_BV(sw);
                    }
                }

                if (pads[sw].padState == IDLE)
                {
                    redLeds&=~_BV(sw);
                    greenLeds&=~_BV(sw);
                    yellowLeds&=~_BV(sw);
                }

        if (pads[sw].sendEnable)
        {
          sendEnable(sw);
          pads[sw].sendEnable=false;
        }

        if (pads[sw].sendLaunch)
        {
          sendLaunch(sw);
          pads[sw].sendLaunch=false;
        }
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

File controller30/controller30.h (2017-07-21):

/*
 * controller30.h
 *
 * Created: 2/26/2014 7:40:38 PM
 *  Author: waynej
 */

#ifndef CONTROLLER30_H_
#define CONTROLLER30_H_

#include "../common/config.h"
#include "../common/zb.h"
#include <avr/io.h>

#define UART_BAUD  9600UL

#define SW1 PORTB0
#define SW2 PORTB1
#define SW3 PORTB2
#define SW4 PORTB3
#define SW5 PORTB4
#define SW6 PORTB5
#define SW7 PORTB6
#define SW8 PORTB7

#define signal1(bit) if(bit) {PORTC|=_BV(1);}else{PORTC&=~_BV(1);}
#define signal2(bit) if(bit) {PORTC|=_BV(6);}else{PORTC&=~_BV(6);}

enum PadState
{
    IDLE, /* We're idle and nothing is happening */
    PRESSED2ENABLE, /*  */
    ENABLED, /*  */
    PRESSED2DISABLE, /*  */
    PAD_LAUNCH /* Launch command received, launch relay is enabled */
};

struct padInfo
{
    enum PadState padState;
    unsigned char padId;
    zbAddr addr;
    zbNetAddr netAddr;
    int statusTimer;
    int enableTimer;
    bool statusValid;
    bool newStatus;
    bool discovered;
    bool discoveredAck;
    bool sendEnable;
    bool sendLaunch;
    int contState;
    int launchState;
    int contResistance;
    int batt;
};

struct NewPad
{
    bool used;
    zbAddr addr;
    zbNetAddr netAddr;
};

#define TIMER0_PERIOD 10

void statusMessage(char * data, int length);
void padDiscovered(zbAddr addr, zbNetAddr netAddr, unsigned char *ni);
void padReady(void);
void initNewPads(void);

#ifdef DEBUG
#define ASSERT(x) if (x) while(true) {};
#else
#define ASSERT(x) 
#endif

#endif /* CONTROLLER30_H_ */

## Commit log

2014-06-19 Initial chechin
    [Batt.xlsx, Cont.xlsx, controller30.dsn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]
2014-06-26 Switch to LCD Display
    [controller30r2.dsn]
2014-07-04 Added linkFSM
    Added LinkFSM to manage link initialization, including setting NI, JV,
    JN, writing to modem NVRAM, and doing a software reset to make sure we
    find a controller.
    [launchFSM.c, linkFSM.c, pad30.c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]
2014-07-10 Added Resistance calculations
2014-08-04 Controller r2
    [controller30r2.csv, controller30r2.dsn, controller30r2.xls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]
2014-08-04 Pad30 r3
    [pad30r3.csv, pad30r3.dsn, pad30r3.xlsx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]
2014-08-04 Added pcb
2014-11-21 Unit tests for r2 controller
    [controller30r21.dsn, pad30r3.dsn]
2014-11-22 Added XBee and ADC test
2014-11-22 Update PCB from build errors
    [pad30r3.csv]
2015-01-26 Added ADC calibration utility
2015-01-26 Fixed value of ADC translation resistor, generated PDF
    [controller30r3.dsn, pad30r3.dsn]
2015-01-26 New ADC regression calculations
    [Batt.xlsx, Cont3.xlsx]
2015-02-01 Add resistance calculations to test
2015-02-01 Add resistance calculations to pad
2015-02-01 New continuity values
    [Cont3.xlsx, controller30r2.csv]
2015-02-17 Updated controller
    [controller30r3.csv, controller30r3.dsn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]
2015-02-17 Updated pad
    [drill_file.drl]
2015-02-17 Other misc changes
    [pad30r4.csv, pad30r4.dsn]
2015-02-17 Add switch doc
2015-04-06 Latest controller schematic
    [controller30r3.dsn]
2015-04-06 Latest pad schematic
    [pad30r4.dsn]
2015-04-06 More pcb cleanup
2015-04-06 Switch to use Bivar LED
    [pad30r4_bom.csv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]
2015-04-07 New calibration tool
    [Cont.xlsx]
2015-06-06 Switch to 16Mhz
2015-06-06 Remove ADC History trace
2015-06-06 Clean up UART
2015-07-08 Added timer on interrupts
2015-08-13 Fix configuration from eeprom issue
    [linkFSM.c, pad30.c]
2015-08-15 new gps project
    [mGPS.dsn]
2015-08-15 new project
    [mGPS.dsn]
2015-08-16 added rf bypass
    [mGPS.dsn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]
2015-08-16 Added pin lables
2015-08-23 Added M10478 GPS
    [mGPS-10478.dsn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]
2015-08-23 Added A2235 GPS
    [mGPS-A2235.dsn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]
2015-08-23 Fixed M10478 pin placement
    [drill_file.drl]
2015-08-30 Added SparkFun GP-735T GPS specs
    [Batt.xlsx, Cont2.xlsx, Cont3.xlsx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]
2015-08-30 Added AAA battery clips
2015-09-07 First crack at GPS receiver
    [mGPSRec.dsn]
2015-09-07 Added keystone battery clip
2015-09-07 New battery connector
    [mGPS2.dsn]
2015-09-08 Switch LCDs, Drop 5v power.
    [mGPSRec.dsn]
2015-09-17 Switch to SMD battery clips
    [mGPS2.dsn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]
2015-09-20 Move chips
    [mGPS-10478.dsn, mGPS-A2235.dsn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]
2015-09-20 Move batteries
    [drill_file.drl]
2015-09-23 Box for mGPSRec
    [mGPSRec.dsn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]
2015-09-24 More Changes for mGPSRec board
    [mGPSRec.dsn]
2015-10-11 Button Fixture
    [mGPS-A2235.dsn, mGPSRec-A2235.dsn, mGPSRec.dsn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]
2015-10-11 Create Button Alignment Guide
2015-12-31 Update design
    [mGPS-A2235.dsn]
2015-12-31 Front Panel Layout
    [panel.dxf]
2015-12-31 Added paste mask
    [drill_file.drl]
2016-01-03 Updates to xbee S2C
    [controller30r3.csv, controller30r3.dsn, pad30r4.csv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]
2016-01-23 Switch to new LCD and Remove 5v power
    [controller30r5.dsn]
2016-02-22 R2 of A2235 GPS
    [drill_file.drl]
2016-02-22 New PCB images
2016-05-24 Added UartTest
2016-05-29 Rotate antenna hole
    [panel.dxf]
2016-06-29 Fix issue with initializing NI for the first time.
    [linkFSM.c, pad30.c]
2016-06-29 New parts list
    [pad30r4.csv, pad30r4.xls]
2016-06-30 Center reference panel
    [panel-cref.dxf]
2016-07-02 Added enclosure
2016-07-03 Updated panel layouts
    [pad-back-panel.dxf, pad-panel.dxf, pad-side-panel.dxf]
2016-11-27 Revision 5 - remove 5v
    [controller30r5.dsn]
2017-05-21 Added 3d printed bushbutton cap for 3FS switches
    [3FS_cap-2.FCStd, 3FS_cap-2.stl, 3FS_cap.FCStd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]
2017-05-21 Change controller 3.0 r5 to controller 3.1
    [controller31r1.csv, controller31r1.dsn, panel-cref.dxf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]
2017-07-16 Fix issue with cold restart not configuring pad properly
    [controller30.c]
2017-07-16 Clean up compile warnings
    [pad30r4.csv, pad30r4.dsn]
2017-07-16 Fix issue with launch command resetting itself on timeout
    [launchFSM.c]
2017-10-23 Added 3d printer templates for controller box patterned after Serpac 17S case
    [17S-controller mod v10.f3d, 17S-controller mod v10.stl]
2017-11-15 Controller case for 3d printer
    [controller-bottom.f3d, controller-top.f3d]
2017-12-05 Added 3d printer case
    [71S-controller mod v25.f3d, 71S-controller mod v25.stl]
2017-12-05 Make sure API setting is correct.
    [linkFSM.c]
2017-12-05 Moved mGPS to new project
    [mGPS-10478.dsn, mGPS-A2235.dsn, mGPS-A2235r2.csv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]
2017-12-05 Clean up 3d printer files
    [17S-controller mod v10.f3d, 17S-controller mod v10.stl, 17S-controller mod v25.f3d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]
2020-02-08 Added pcb pdf
2021-12-22 Attempt to standardize on power connector
    [controller31r1.dsn]
2021-12-31 Enable timer task
2022-01-03 Added pad led code.
2022-01-05 Converted the remaining zb driver senders
2022-01-08 Switch to ATMega644
2022-01-11 Reinstate timer.
2022-01-24 Added Switch API
